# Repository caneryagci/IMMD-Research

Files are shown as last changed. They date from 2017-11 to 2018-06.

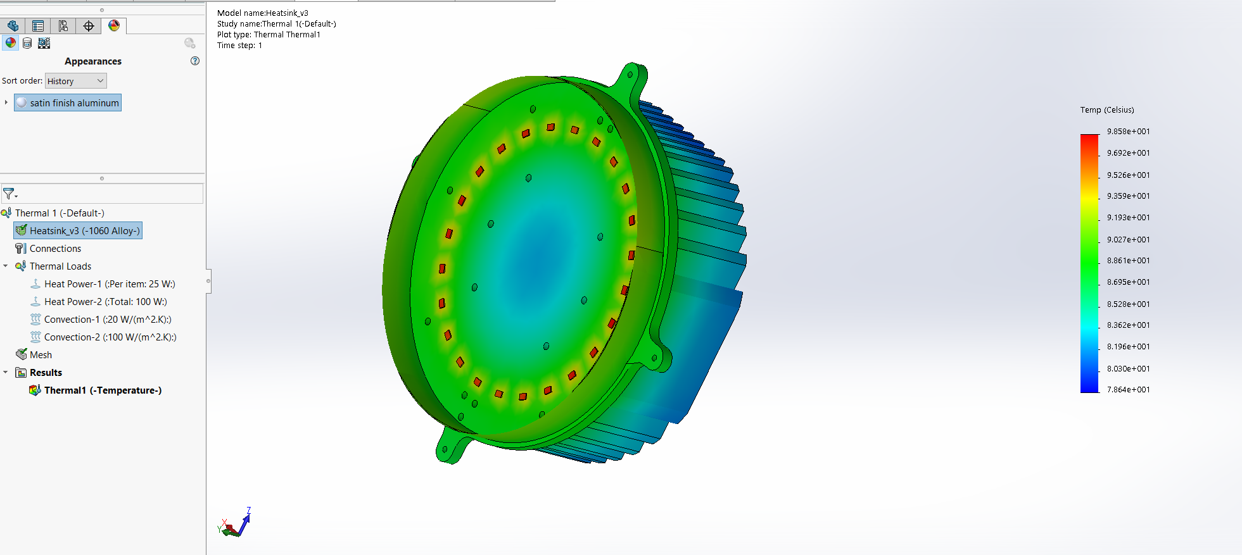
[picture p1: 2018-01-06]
Heatsink CAD Design/Design 3/Ekran Alıntısı.PNG

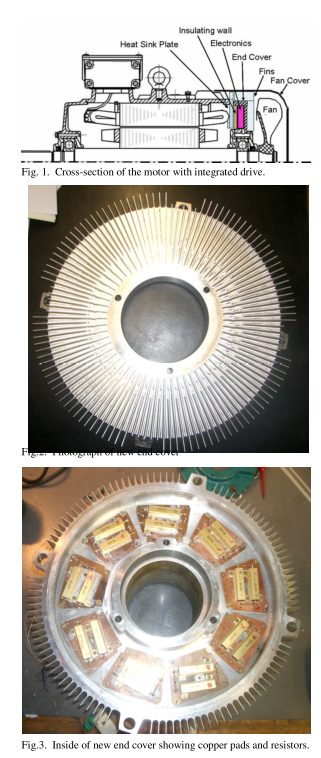
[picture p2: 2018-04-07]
Presentations/14.11.2017/Ekran Alıntısı.PNG

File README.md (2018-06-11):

# Thermal modeling, analysis and design of an Integrated Modular Motor Drive Application
The aim of the project is to obtain a thermal model of an integrated modular motor drive having different heat sources, analyze the thermal behavior of individual parts. A natural cooled heatsink is developed for the system. FEA and Steady-State Lumped Parameter analysis are implemented on Solidworks and MATLAB/Simulink.

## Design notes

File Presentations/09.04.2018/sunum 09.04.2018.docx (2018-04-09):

Steady-state Lumped Parameter Analysis

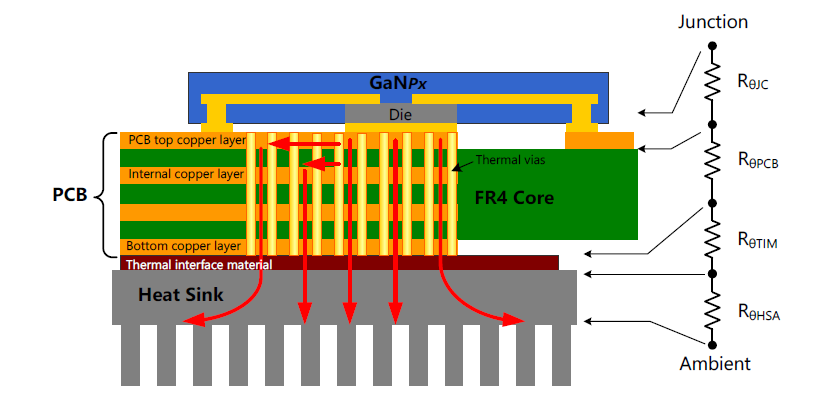
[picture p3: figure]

- 123 Thermal via (0.3mm diameter) , 6 Layer PCB, Rjc= 0.5 Ω , Rcpb= 4.5Ω(1.6mm & 6 layer), RTIM = 1.5 Ω

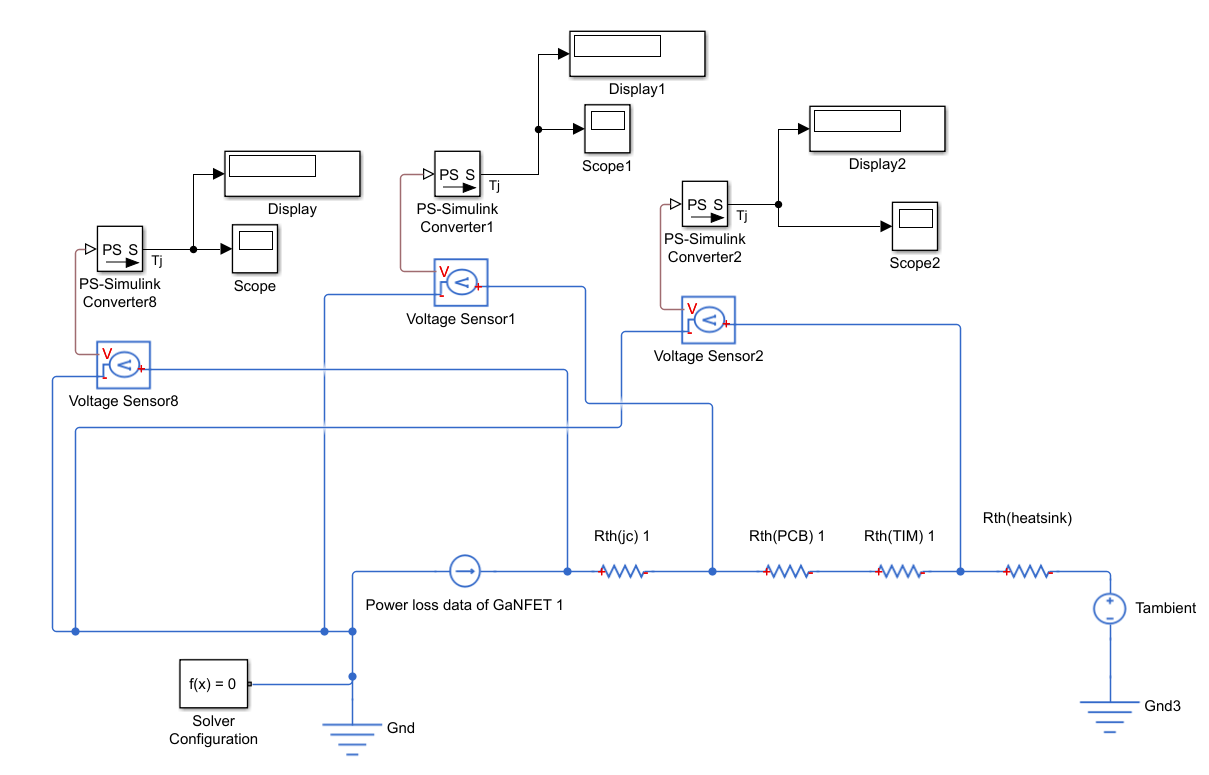
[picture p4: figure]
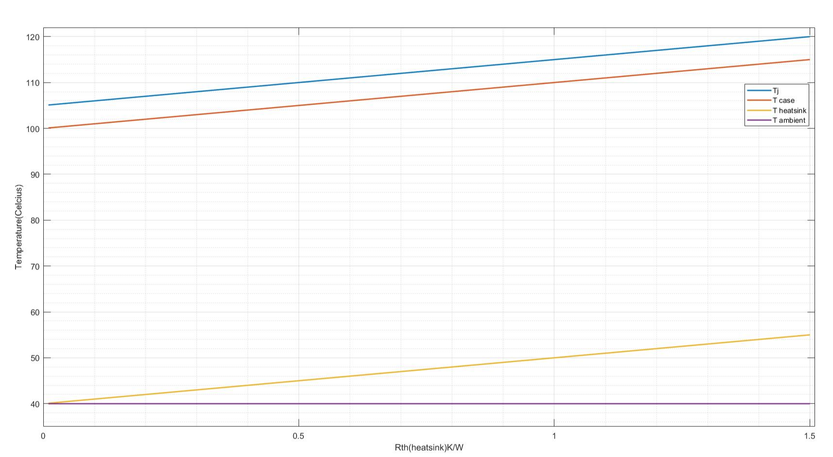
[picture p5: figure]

https://www.myheatsinks.com/calculate/thermal-resistance-plate-fin/

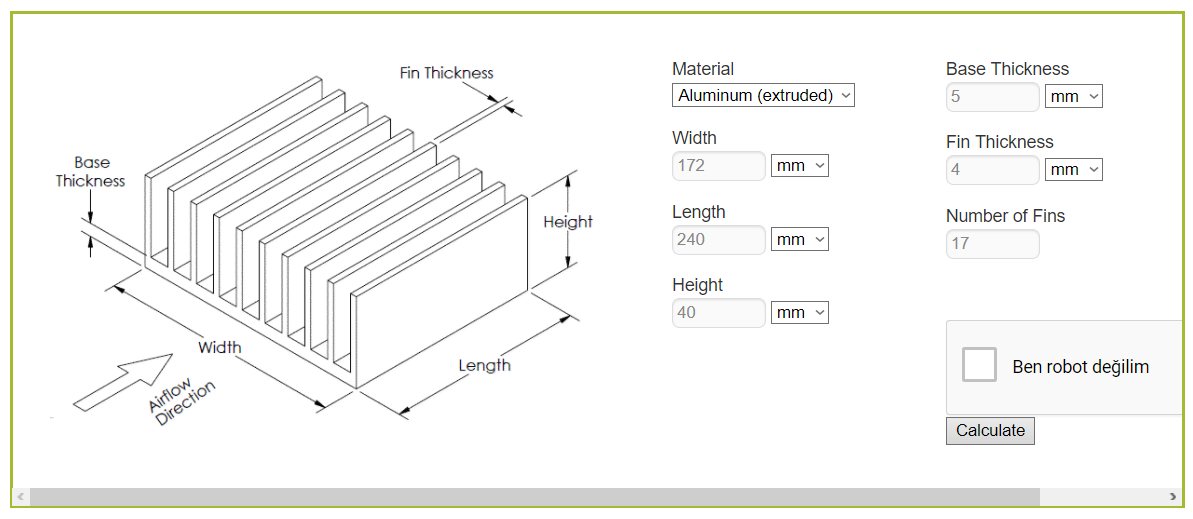
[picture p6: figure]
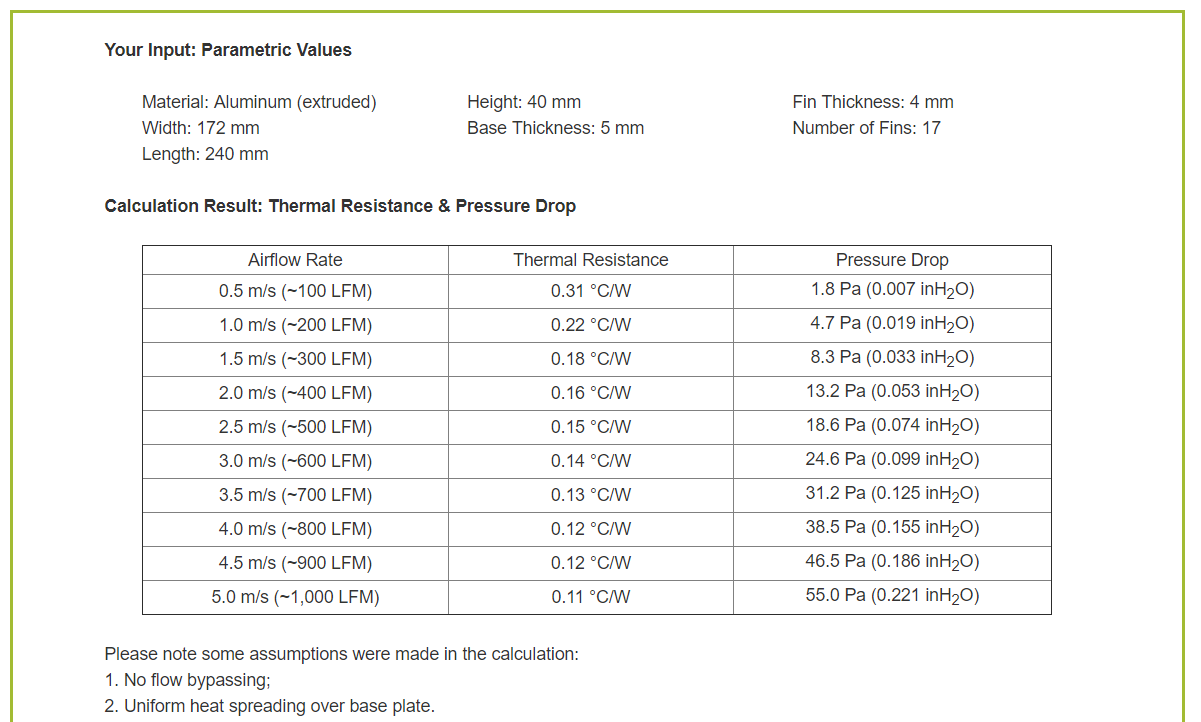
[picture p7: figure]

- The results changes between Rth (heatsink)= 0.25 - 0.45 ℃/W

FEA Analysis (Steady State)

If you think that GanFET is a black box with 0.5 Rjc ;

- L is the thickness (m) (thickness of the package and the thermal pad);
- A is the effective contact area (m²) (Area of the thermal pad) ;
- k is the conductivity of the box (W/(m*K))

R= L/(A.k) (1)

k=L/(A.R)=(0.440 x 10^(-3))/(2.667 x 10^(-3) x 0.5)=32.99 W/(m.K)

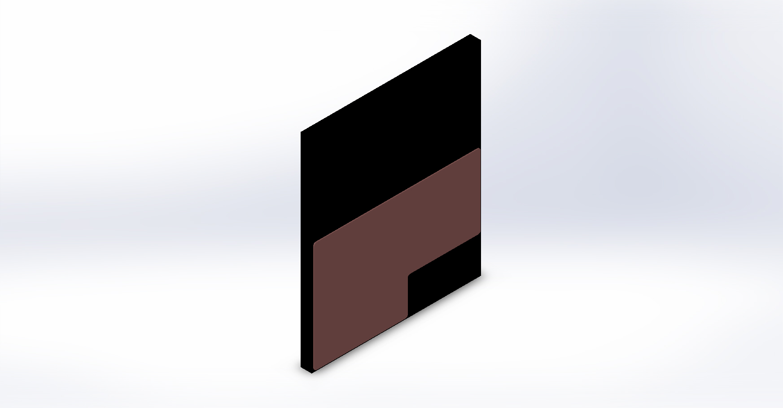
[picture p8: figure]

- For the most accurate Heat convection coefficients CFD analysis required.

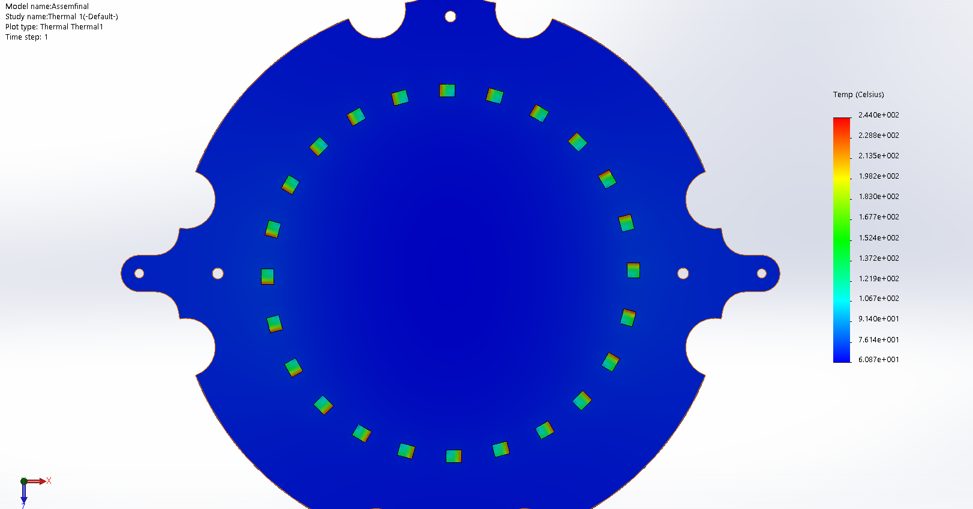
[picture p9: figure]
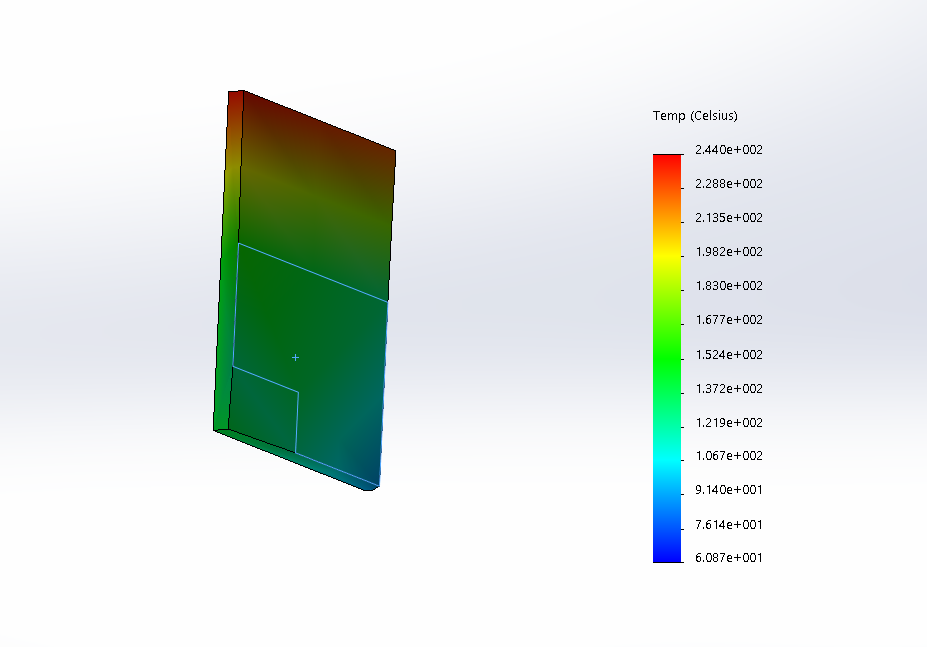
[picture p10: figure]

3D Design Engineers are divided into 2 groups;

- MCAD Design engineer (Mechanical)
- ECAD Design Engineer (Electronic)
- These engineers share the common file that is in IDF, EMN or STEP format.
- Each format has different features. (Based on the PCB layout and holes)
- IDF is the most common.

Following weeks;

- More accurate results
- FEA Transient Analysis

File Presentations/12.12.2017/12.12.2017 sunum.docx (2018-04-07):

- In fact, the heat-sink that was installed in this inverter has not a known value of thermal resistance. Anyway, to resolve this problem, is possible to measure this parameter measuring at the same time the losses and the temperature of the heat-sink for different values of losses. Once this parameter is found it is possible to simulate the real working condition in the model and to compare correctly the results.

[1] FOSSATO, F. (2014). Loss estimation in a voltage source inverter for electrical drives. University of Padua.

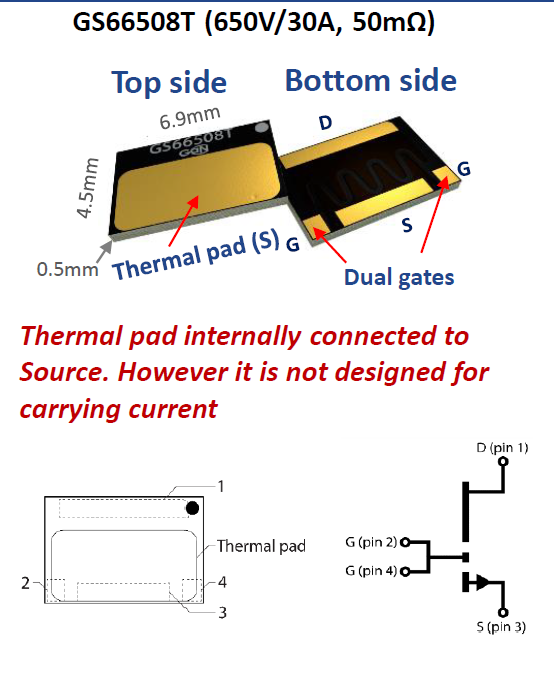
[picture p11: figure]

Figure: Top cooled

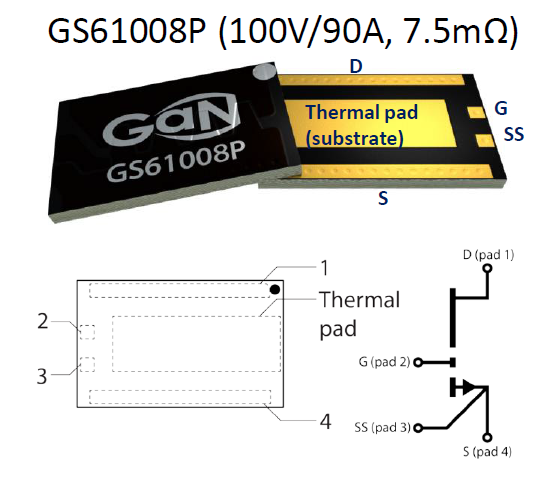
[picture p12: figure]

Figure: Bottom cooled

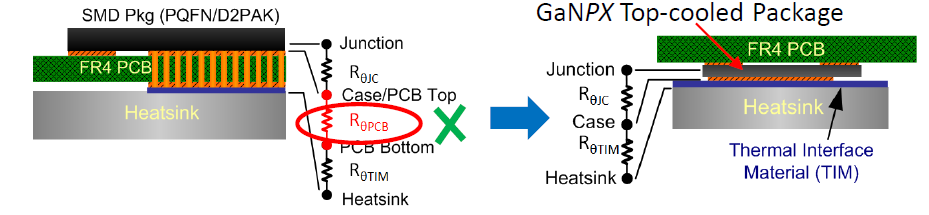
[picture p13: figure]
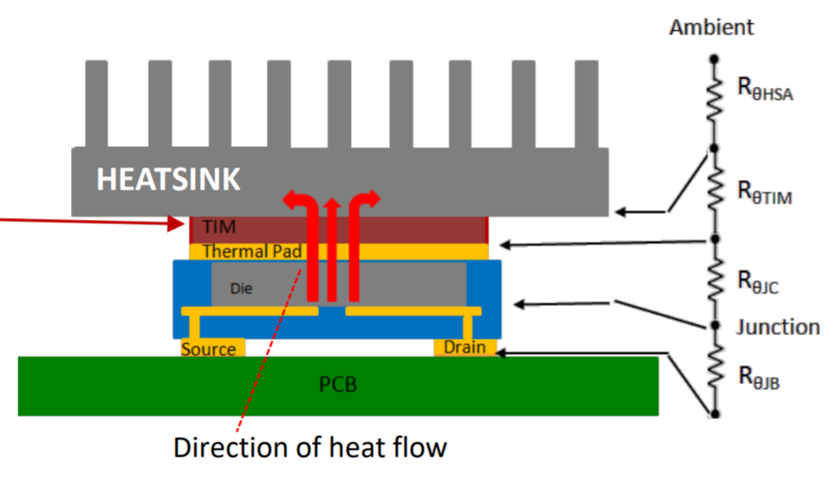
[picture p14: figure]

Figure: Top side cooling

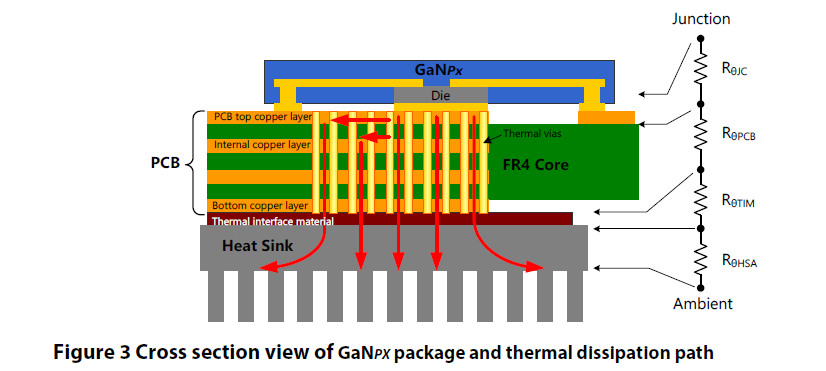
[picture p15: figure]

Figure:Bottom side cooling

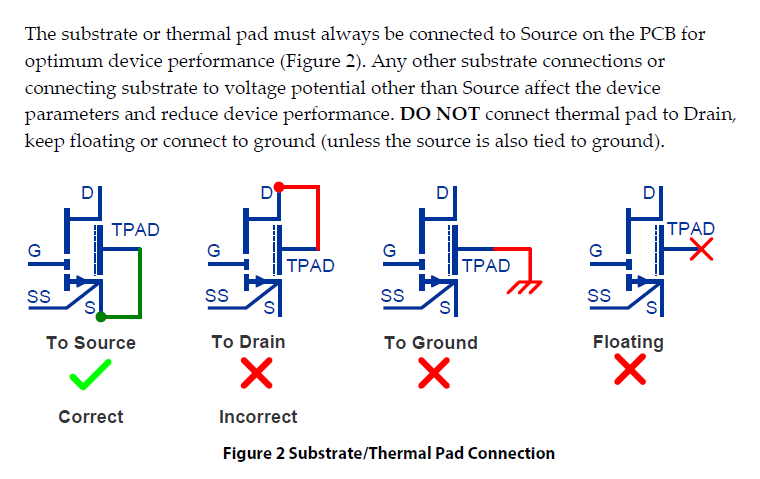
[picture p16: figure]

PCB thermal performance

1. Heat spreading copper pad

The top copper pad plays important role to conduct the heat from the small area under the device to larger area on the PCB. As such, the top copper layer must have sufficient thickness and area to provide enough heat spreading. It is recommended to always use 2 oz (56.7 g) or thicker copper on all layers. The internal and bottom layers also improve the heat spreading. The bottom copper pad serves as the contact surface to the heatsink or Thermal Interface Material (TIM) and it should have sufficient coverage to allow optimum heat transfer to the heatsink.

2. Thermal vias

The most effective way to improve vertical heat transfer for FR-4 PCB is to add plated through-hole thermal vias between conductive layers. Since FR-4 material has very low thermal conductivity, thermal vias design is one of the dominating factors for total PCB thermal resistance.

Below are some considerations for thermal vias design:

• Adding open plated through vias to the SMT pad (“Via In Pad”) is generally not a common practice as it may create the solder-wicking issue: the solder tends to be drained down into the vias during the reflow process and generates solder voids on the pad. Following steps can be taken to limit this problem:

o Use small via diameter. The surface tension of solder limits the amount of solder wicking on smaller vias. With 0.3 mm or smaller via diameter, the solder wicking can be reduced.

o Fill the vias with thermally conductive materials. It eliminates the solder wicking but adds cost and extra manufacturing step.

• 8 mil (0.2 mm) is typical minimum mechanical drilling size. 12 mil (0.3 mm) is more common and lower cost.

• IPC-6012 specifies minimum 0.8 mil (20 μm) copper plating thickness for Class 2 PCB and 1 mil (25 μm) is standard via plating thickness.

GaN Systems Simulation

The first step is to determine the right size for the heat spreading copper pad and how many vias are needed under the thermal pad.

The design constraint rule is that no vias are added towards the drain side in order to maintain the same clearance between thermal and Drain pads. Also the left edge of the copper pad keeps minimum 0.5 mm distance from Gate and Source-sense pads. There will be no vias added on the left side the package as that area is typically used for gate driver circuit.

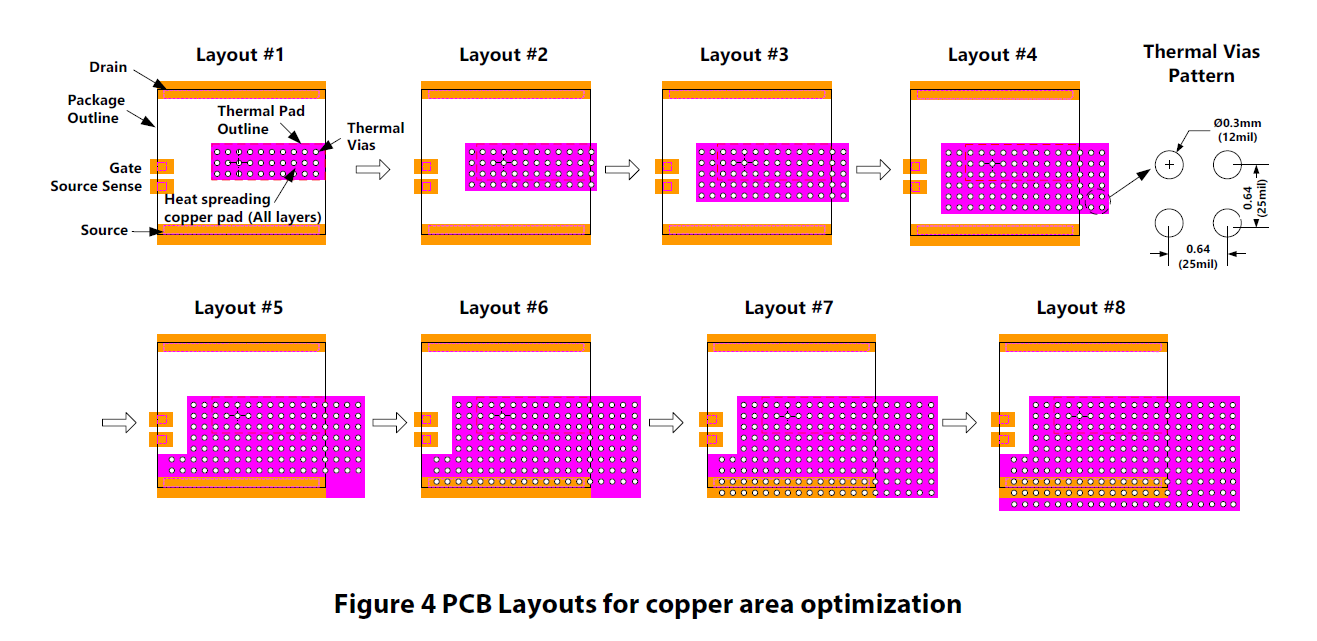
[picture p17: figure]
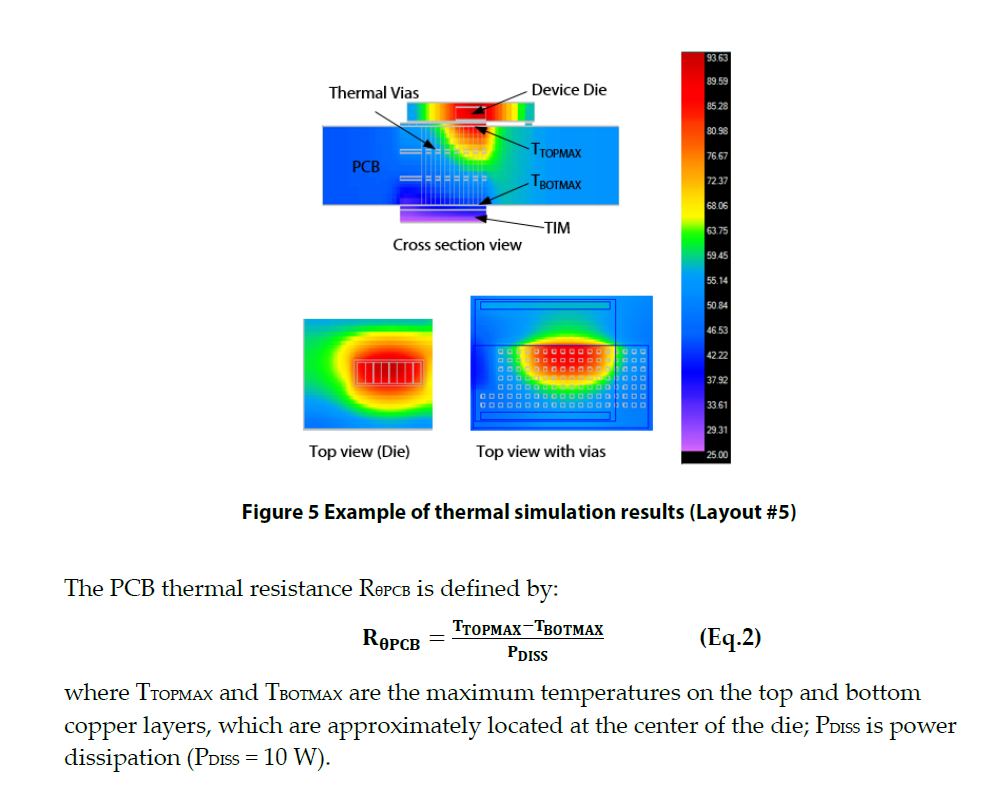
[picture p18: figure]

Figure: ElectroFlo® thermal analysis software was used for the thermal simulation

Both PCB and TIM thermal resistances decrease with the increasing of via numbers and copper area. When number of thermal vias increase from 30 to 210 (Layout #1 to #8), the PCB thermal resistance RθPCB drops almost 2.4 times from 11.5 °C/W to 4.8 °C/W. The TIM thermal resistance RθTIM also reduces about 3 times as the contact area increases.

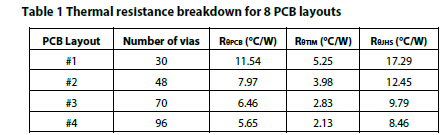
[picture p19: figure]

For optimum PCB thermal performance, it is recommended that the copper pad and thermal vias should cover at least 10x 5 mm area (50 mm2) under the thermal pad (or approximately 120 thermal vias), as shown in Figure 7.

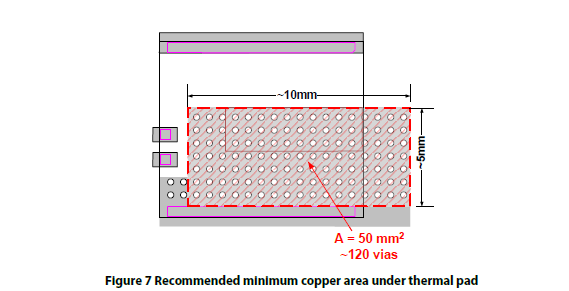
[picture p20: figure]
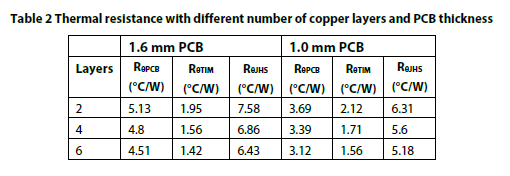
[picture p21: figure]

PCB thickness has

- less effect on TIM thermal performance and actually increases TIM thermal resistance by about 10 %.

- improvement on PCB thermal resistance

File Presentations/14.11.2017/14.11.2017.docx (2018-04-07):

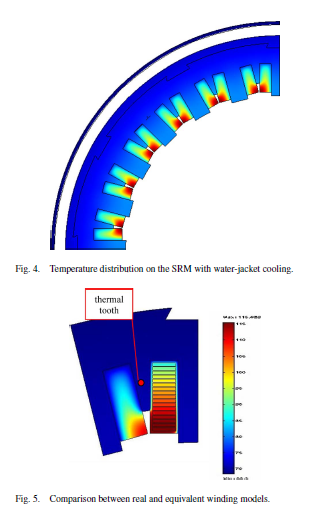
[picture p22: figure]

Since the copper–iron thermal resistance is the largest one in the thermal equivalent circuit of the machine, the reduction of the temperature gradient between copper and iron significantly reduces the total temperature gradient between the copper and the cooling fluid. For this reason, an auxiliary “thermal tooth” (Fig. 5) made of iron has been inserted to fill the triangle area: The iron triangles increase the thermal contact surface, improving the heat transmission through the coils sides, with only a little influence in torque production, if the height of a thermal triangle is sufficiently small.

[Tenconi, A., Profumo, F., Bauer, S. E., & Hennen, M. D. (2008). Temperatures evaluation in an integrated motor drive for traction applications. IEEE Transactions on Industrial Electronics, 55(10), 3619–3626. https://doi.org/10.1109/TIE.2008.2003099]


The thermal sink is common to all heat sources (Motor & Power Electronics).

In parallel configuration, the thermal flux paths are independent and do not influence each other. In practice, when the two heat sources are in close proximity this may require some thermal isolation.

Thermal isolation layer must be inserted to stop any thermal interference from the end-winding losses.

Series configuration would be difficult to achieve since the thermal gradient between the machine and the power electronics must be carefully managed so as not to overheat the devices.

The annular region surrounding the bearing housing on the end cover at the fan-end of the motor probably will be selected as being the most suitable for the drive components. Because the advantage that a flat area could be created to mount the components that could be largely isolated thermally from the rest of the motor and that could easily be cooled by air from the fan.

To prevent over heating of the end windings, an additional heat sink plate must be manufactured to fit between the end cover and the frame of the motor to conduct heat from the end region.

This heatsink plate effectively performed to replace the end cover in dissipating heat from the end region of the motor.

[Pickering, S., Thovex, F., Wheeler, P., & Bradley, K. (2006). Thermal Design of an Integrated Motor Drive. IECON 2006 - 32nd Annual Conference on IEEE Industrial Electronics, 4794–4799. https://doi.org/10.1109/IECON.2006.348109]

Heatsink

Fan

Power Electronics

Motor

Parallel Configuration

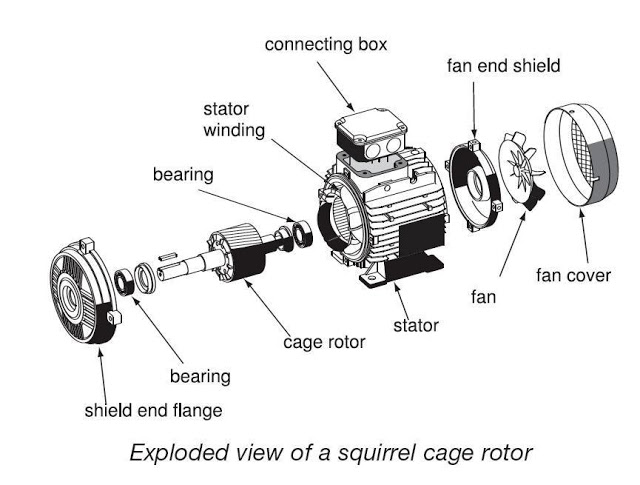
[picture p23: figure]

Thermal Insulation Layer

End Windings + Heatsink plate of the motor

Annular Heatsink

Power Electronics

Fan

Fan end shield

Variables:

- Fin density & length in the direction of the flow
- Fan Flow rate (velocity)
- Diameter of the heatsink in the direction perpendicular to the flow

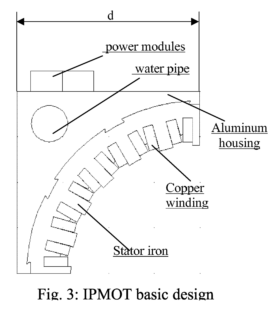
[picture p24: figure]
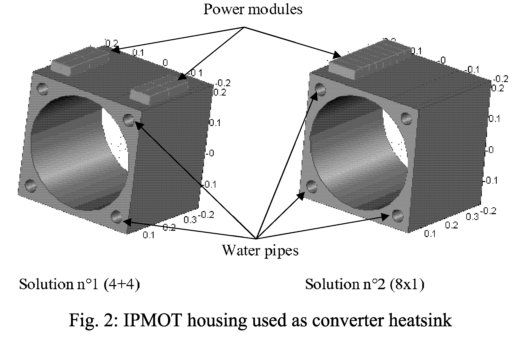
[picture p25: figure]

- Uses a rectangular profile machine with sunken cooling pipes in the machine core-back.
- The purpose of the flat edge profile of the machine is to provide a fixing surface directly on the machine body for the power electronic components.

[Farina, F., Rossi, D., Tenconi, A., Profumo, F., & Bauer, S. E. (2005). Thermal design of integrated motor drives for traction applications. 2005 European Conference on Power Electronics and Applications, 1–10. https://doi.org/10.1109/EPE.2005.219711]

PLAN:

1- Build a steady-state lump parameter circuit & simulate.
2- Determine a Rth value.
3- Design an annular heatsink by determining the critical parameters.
4- Simulate the heatsink by using thermal simulation software.

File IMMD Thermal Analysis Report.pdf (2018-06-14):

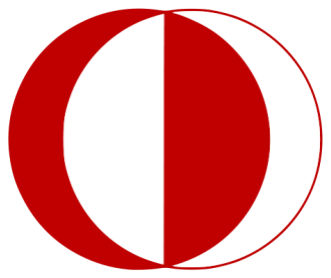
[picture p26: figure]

### MIDDLE EAST TECHNICAL UNIVERSITY

### DEPARTMENT OF ELECTRICAL AND ELECTRONICS ENGINEERING

### THERMAL MODELLING, ANALYSIS AND DESIGN OF AN INTEGRATED MODULAR MOTOR DRIVE APPLICATION

## Bekir Caner YAĞCI

## E:caneryagci1@gmail.com

P: +90 535 977 5608

14.06.2018

### Table of Contents

### 1. Introduction

The aim of the project is to obtain a thermal model of an integrated modular motor drive having different heat sources such as; power semiconductors, integrated circuits, capacitors, motor windings etc., and analyse the thermal behaviour of individual parts. A natural cooled heatsink is developed for the system. FEA and Steady-State Lumped Parameter analysis are implemented on SolidWorks and MATLAB/Simulink whether the designed heatsink reach the criteria.

In this report, theoretical and practical knowledge about the project is shared. Firstly, basic heat transfer mechanism, the ways of thermal analysis, and thermal resistance calculation is explained. Then, implemented analysis, their results, and practical challenges that encountered during analysis are discussed. Finally, supplementary links and articles are given in the references part.

### 2. Heat Transfer Mechanism & Thermal Analysis Methods

There are three mechanisms of heat transfer. These mechanisms are:

### 1. Conduction

- Conduction is responsible for heat transfer inside a solid body (or solid body to solid body assuming 100% conduction between).

### 2. Convection


- Convective heat transfer is the heat flow between a solid body and the surrounding fluid (either liquid or gas).


- It can be either natural or forced convection.

- The magnitude of the convection coefficient strongly depends on the medium (fluid) surrounding a solid body.


Figure 1: Convection coefficients for different media

### 3. Radiation

- Radiation heat transfer occurs between a solid body and the ambient or between two solid bodies without presence of any medium (fluid).
- Radiation is usually ignored since it has less effect than conduction, convection, and difficult to estimate.


Also, there are three methods of thermal analysis. These methods are:

### 1. Steady-State Lumped Parameter

- It is the method of thermal equivalent circuit of the interior of the system. This is analogous to an electric circuit, in that heat is generated by "current sources" that is the power loss and temperature is analogous to voltage. The rate of generation of heat in a source is measured in Watts. The heat flow rate, which is also measured in Watts, is analogous to current. Resistance is measured in ℃/W.
- It is the most straightforward method.
- Capacitive and the inductive effects in the system can be ignored to analyse the steady-state behaviour of the system. Thus, only a resistive circuitry could be analyse to see the worst case scenario of the system.

### 2. Finite Element Analysis (FEA)

- Well recognized tool used in the analysis of heat transfer problems.

- However, FEA can only analyze solid bodies and, by necessity thermal analysis with FEA is limited to conductive heat transfer. The other two types of heat transfer: convection and radiation must by approximated by boundary conditions.
- Requires a simulation program. (SolidWorks)

### 3. Computational Fluid Dynamics (CFD)

- Modeling all three mechanisms of heat transfer without arbitrary assumption requires a combined use of FEA and Computational Fluid Dynamics (CFD).
- CFD is the most complex computation method.
- Requires a simulation program. (SolidWorks Flow Simulation, ANSYS Fluid Dynamics, etc.)

Beside the lumped parameter method, the method to use depends on the heat transfer mechanisms that are taking place in the components that you are designing: conduction, convection, radiation or a combination of them. In addition, the level of accuracy you are willing to accept will also influence your decision.

The table below summarizes the method to use depending on the type of heat transfer mechanisms you are analyzing:

Table 1: The tool to use depending on the type of heat transfer mechanisms analysed


Thermal resistance calculation for heatsink

Fin geometry, fin length, number of fins, material (usually aluminium), cooling (natural or forced), heatsink geometry are effective on the thermal resistance of the heatsink.

For the calculation of the thermal resistance of the heatsink an online calculator at “https://www.myheatsinks.com/calculate/thermal-resistance-plate-fin/” is used to hardly estimate the thermal resistance of the heatsink selected. Also, the datasheets of the selected heatsinks are controlled if they meet the thermal resistance range calculated in the steady state analysis.

For the analytical calculation of the heatsink thermal resistance see reference [12].

### 3. Steady-State Lumped Parameter Analysis

To implement the steady-state analysis on Simulink environment thermal resistance values are selected from the Gan System’s own application notes. For more information see reference [5].

Given conditions are shown below;

- 120 Thermal via (0.3mm diameter)
- 6 Layer PCB
- Rjc= 0.5 Ω
- Rcpb= 4.5Ω(1.6mm & 6 layer)
- RTIM = 1.5 Ω


Figure 2: Bottom cooled GanFET connection

Figure 2 shows the lumped parameter circuitry of the bottom cooled GanFET. This circuit is drawn in Simulink environment as shown in the figure 3 with the given thermal resistance values. Then, voltage measurements are taken as temperature data from junction, case and heatsink. Ambient temperature is selected as 40 ℃. Finally, the Matlab code in appendix part is run to sweep the Rth(heatsink) parameter, and the results are plotted in figure 4.


Figure 3: Steady-state Simulink model

The result of the analysis is shown in figure 4. According to the figure 4, junction temperature is 110 ℃ when the thermal resistance of the heatsink is 0.5℃/W. Thus, the thermal resistance of the selected heatsink must be less than or equal to 0.5℃/W approximately.

Figure 4: Temperature results

For the simulation files see reference [11].

### 4. FEA Analysis

FEA analysis is implemented on SolidWorks environment. For the implementation of the analysis a 3D CAD figure of a circular heatsink with 40mm fin length, 5 mm baseplate thickness, 150 cm radius is drawn. Holes for mounting and places for windings are cut. Aluminium alloy is selected as material. For the CAD Drawings and the thermal analysis results see reference [11]. To learn more about the SolidWorks thermal analysis see reference [3], [4]

With SOLIDWORKS Simulation which uses finite element method, only heat transfer by conduction is modeled directly. Convection and radiation are modeled as boundary conditions. This is done by defining convection and/or radiation coefficients. Thus, a convection coefficient between 5-25 ℃/W must be defined to imitate natural cooling condition. Also, 6℃/W thermal resistance is defined via contact set to resemble the PCB and the TIM between each GanFET and the heatsink[4].


Figure 5: Overall heat dissipation on heatsink

The 3D drawing of the GanFET is available online or be see reference [11]. It can also be drawn with the given dimensions in the datasheet. For the thermal analysis only the thermal pad layer and the case is considered and the other layers such as drain, gate, soldering layers are ignored, since they increase the computation time and usually cause mesh errors.

GanFET is assumed to be a black box with a 0.5℃/W (create material with this specification) thermal resistance, and only conduction between the Gan’s and the heatsink is from the thermal pad in the implemented analyze. Figure 6 shows the heat dissipaton on GanFET. Blue line in figure 6 is the thermal pad, and it shows that the conducted part of the GanFET is cooled and the operation is possible with this heatsink as long as the proper conduction between the heatsink and the GanFET is implemented. However if the conduction between the heatsink and the GanFET is not proper GanFET can be heated up to 244 ℃.


Figure 6: Heat dissipation on a single GanFET

Problems of FEA in SolidWorks

The problem is that the SolidWorks is designed for mechanical systems and it is not very easy to reach the most accurate solution if you draw the electronic components such as GanFET, PCB, etc. in SolidWorks, since it is a bit complicated. My advice is to design the 3D Drawings of the electronic components in another simulation program such as Altium, and combine mechanical parts and the electronic parts via import/export in SolidWorks/CircuitWorks.

### 5. References

[1] Abebe, R., Vakil, G., Calzo, G. Lo, Cox, T., Gerada, C., & Johnson, M. (2015). FEA based thermal analysis of various topologies for Integrated Motor Drives (IMD). In IECON 2015 - 41st Annual Conference of the IEEE Industrial Electronics Society (pp. 001976–001981). IEEE. https://doi.org/10.1109/IECON.2015.7392390
[2] Pickering, S., Thovex, F., Wheeler, P., & Bradley, K. (2006). Thermal Design of an Integrated Motor Drive. IECON 2006 - 32nd Annual Conference on IEEE Industrial Electronics, 4794– 4799. https://doi.org/10.1109/IECON.2006.348109
[3] http://blogs.solidworks.com/solidworksblog/2017/04/use-fea-vs-cfd-thermal-analysis.html
[4] https://www.youtube.com/watch?v=Z8ymNlJoitw&list=WL&t=0s&index=45
[5] https://gansystems.com/design-center/application-notes/
[6] https://kupdf.com/embed/miller-tje-speed39s-electric-motors_58b2bb6a6454a7ce1eb1eaad.html?sp=%7Bstart%7D (https://kupdf.com/embed/miller-tje-speed39s-electric-motors_58b2bb6a6454a7ce1eb1eaad.html?sp=%7Bstart%7D)
[7] Mueller, S. I. (2005). MODEL AND DESIGN OF AN AIR-COOLED THERMAL MANAGEMENT SYSTEM FOR AN INTEGRATED MOTOR / CONTROLLER by.
[8] Inverter, S., Zhao, C., Member, S., Trento, B., Jiang, L., Member, S., … Langley, R. (2016). Design and Implementation of a GaN-Based , 4(3), 824–840.
[9] Wang, J., Li, Y., & Han, Y. (2015). Integrated Modular Motor Drive Design With GaN Power FETs. IEEE Transactions on Industry Applications, 51(c), 3198–3207. https://doi.org/10.1109/TIA.2015.2413380
[10] Tenconi, A., Profumo, F., Bauer, S. E., & Hennen, M. D. (2008). Temperatures evaluation in an integrated motor drive for traction applications. IEEE Transactions on Industrial Electronics, 55(10), 3619–3626. https://doi.org/10.1109/TIE.2008.2003099
[11] https://github.com/caneryagci/IMMD-Research
[12] Factor, P., & Perimeter, P. (n.d.). SIMPLIFIED METHOD FOR ESTIMATING HEAT SINK THERMAL RESISTANCE - Ө SA MATHEMATICAL FORMULA ANALYSES, 1–7.

Appendix: Steady-State Lumped Parameter Matlab Plot Code

Power_loss = 10;
Rth_jc = 0.5;
Rth_pcb = 4.5;
R_tim = 1.5;
T_ambient = 40;
ambient_t = ones(150,1)*40; junc_temp = zeros(150,1);
case_temp = zeros(150,1);
heatsink_t = zeros (150,1); resistance_h= zeros(150,1);

open_system('thermal_model'); for i= 1:1:150
Rth_heatsink = 0.01*i; %K/W sim('thermal_model');
resistance_h(i) = Rth_heatsink; junc_temp(i)= Tj(51,2);
case_temp(i) = T_case(51,2); heatsink_t (i) = T_heatsink(51,2);
end

plot(resistance_h,junc_temp,resistance_h,case_temp,resistance_h,heatsink_t,resistance_h,ambient_t,'L ineWidth',1.5);
grid on;
grid minor;
legend('Tj','T case','T heatsink','T ambient','Location','northeast'); xlabel('Rth(heatsink)K/W');
ylabel('Temperature(Celcius)');
ylim([35 122]);
xlim([0 1.51]);

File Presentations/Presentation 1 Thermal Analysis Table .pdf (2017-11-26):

Parameters | Values | Units
Rth (j-c) IGBT | 0.066 | K/W
Rth(j-c) FWD | 0.120 | K/W
Rth(case)1 | 0.000001 | K/W
Rth(case)2 | 0.000001 | K/W
Rth(case)3 | 0.000001 | K/W
Rth(paste) | 0.015 | K/W
Rth(heatsink) | 0.005 – 0.05 | K/W
Pss | 116.065 | W
Psw | 116.18 | W
Total Power loss of each IGBT | 232.25 | W
PDC | 30.54 | W
Prr | 11.25 | W
Total Power loss of each FWD | 41.79 | W
Esw(on) | 41 | mJ
Esw(off) | 32 | mJ
Fsw | 5 | kHz
Icp | 300 | A
VCE(sat) | 2 | V
VEC | 1.8 | V

D 0.85
θ | 25.842 | Degrees
Irr | 200 | A
trr | 300 | ns
VCE(pk) | 300 | V


Pss: Steady-state loss per switching IGBT

Psw: Switching loss per switching IGBT

PDC: Steady-state loss per diode

Prr: Recovery loss per diode

Rth (j-c): thermal resistance junction to case

Tj IGBT 1U: Junction temperature of the upper IGBT of the phase 1

Tj IGBT 1L: Junction temperature of the lower IGBT of the phase 1

Tj FWD 1U: Junction temperature of the upper free-wheeling diode of the phase 1

Tj FWD 1L: Junction temperature of the lower free-wheeling diode of the phase 1

Data | Rth(heatsink) K/W | Tj IGBT (celcius) | Tj FWD(celcius) | T(case) | T(heatsink) | Ta
1 | 0.005 | 75.64 | 100.8 | 72.88 | 48.22 | 40
2 | 0.006 | 77.29 | 102.4 | 74.53 | 49.87 | 40
3 | 0.007 | 78.93 | 104 | 76.17 | 51.5 | 40
4 | 0.008 | 80.58 | 105.7 | 77.82 | 53.15 | 40
5 | 0.009 | 82.22 | 107.3 | 79.46 | 54.8 | 40
6 | 0.010 | 83.66 | 109 | 81.11 | 56.44 | 40
7 | 0.012 | 87.15 | 112.3 | 84.39 | 59.73 | 40
8 | 0.015 | 92.09 | 117.2 | 89.33 | 64.66 | 40
9 | 0.017 | 95.37 | 120.5 | 92.62 | 67.95 | 40
10 | 0.020 | 100.3 | 125.4 | 97.55 | 72.88 | 40
11 | 0.022 | 103.6 | 128.7 | 100.8 | 76.17 | 40
12 | 0.025 | 108.5 | 133.6 | 105.8 | 81.11 | 40
13 | 0.027 | 111.8 | 136.9 | 109.1 | 84.39 | 40
14 | 0.030 | 116.7 | 141.9 | 114 | 89.33 | 40
15 | 0.032 | 120 | 145.1 | 117.3 | 92.62 | 40
16 | 0.035 | 125 | 150 | 122.2 | 97.55 | 40
17 | 0.037 | 128.3 | 153.4 | 125.5 | 100.8 | 40
18 | 0.040 | 133.2 | 158.3 | 130.4 | 105.8 | 40
19 | 0.042 | 136.5 | 161.6 | 133.7 | 109.1 | 40
20 | 0.045 | 141.4 | 166.5 | 138.7 | 114 | 40
21 | 0.047 | 144.7 | 169.8 | 141.9 | 117.3 | 40
22 | 0.050 | 149.6 | 174.7 | 146.9 | 122.2 | 40


- Tj(FWD) = 125.4 ℃ when Rth(heatsink) = 0.02 K/W

### Heatsink Selection



### QUESTION ?



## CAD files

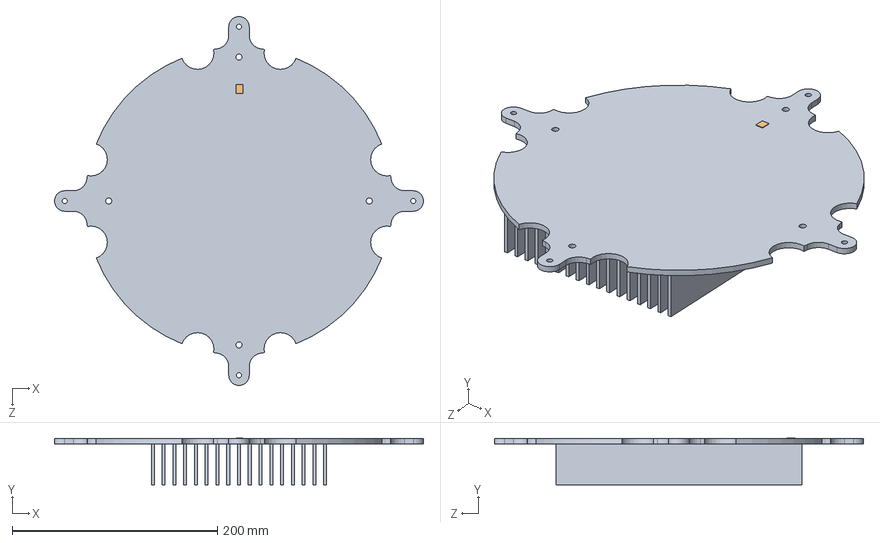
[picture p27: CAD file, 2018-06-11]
FEA Analysis 2/Assem3.SLDASM
360.0 x 45.5 x 360.0 mm
Heatsink2
Package
PCB Bottom CDMM

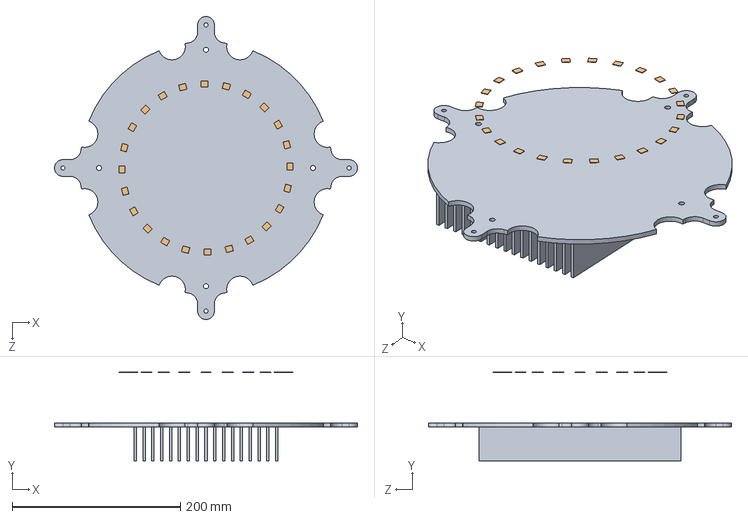
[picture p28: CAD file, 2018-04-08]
FEA Analysis 1/Assemfinal.SLDASM
360.0 x 105.4 x 360.0 mm
Heatsink
Black Box x 24

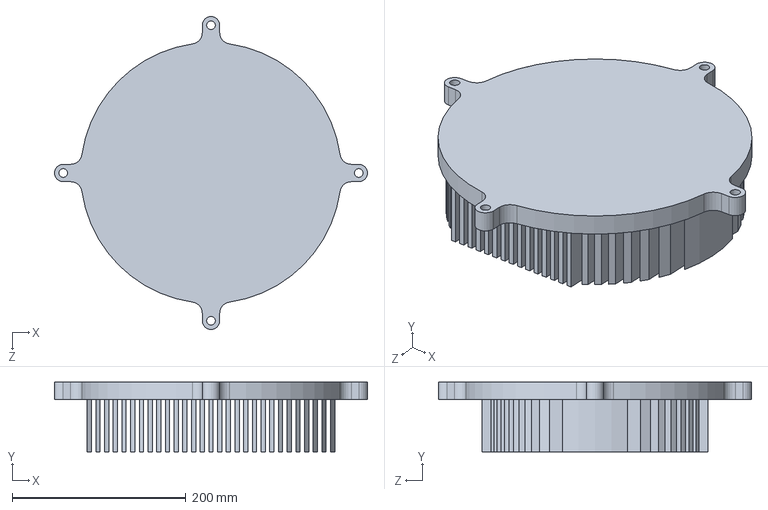
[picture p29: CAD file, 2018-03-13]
Heatsink CAD Design/Design 1/Heatsink_v1.SLDPRT
360.0 x 80.0 x 360.0 mm

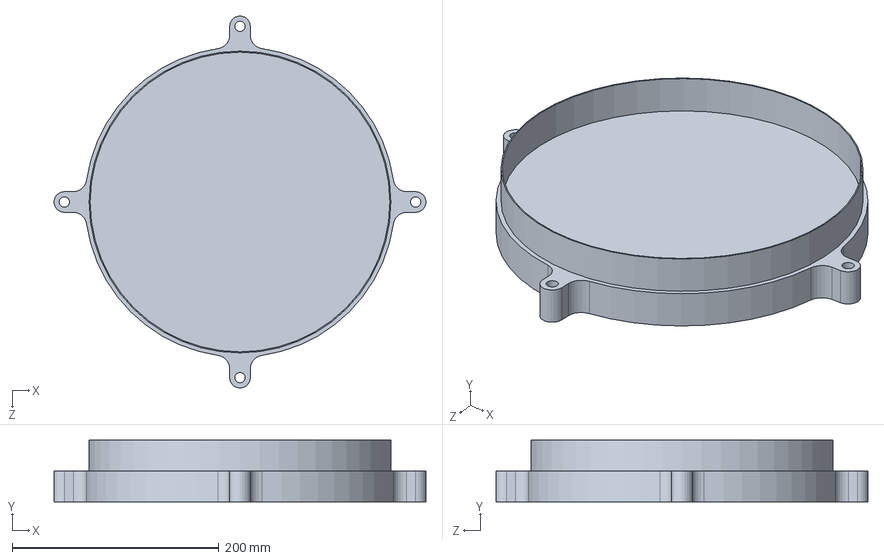
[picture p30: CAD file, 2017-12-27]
Heatsink CAD Design/Design 2/Heatsink2.SLDPRT
360.0 x 60.0 x 360.0 mm

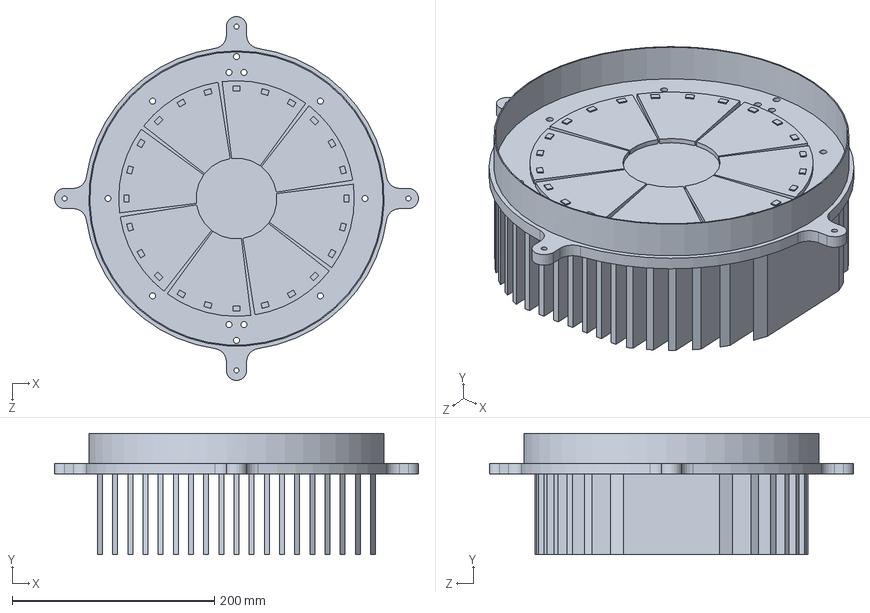
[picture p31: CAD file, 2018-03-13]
Heatsink CAD Design/Design 3/Heatsink_v3.SLDPRT
360.0 x 120.0 x 360.0 mm

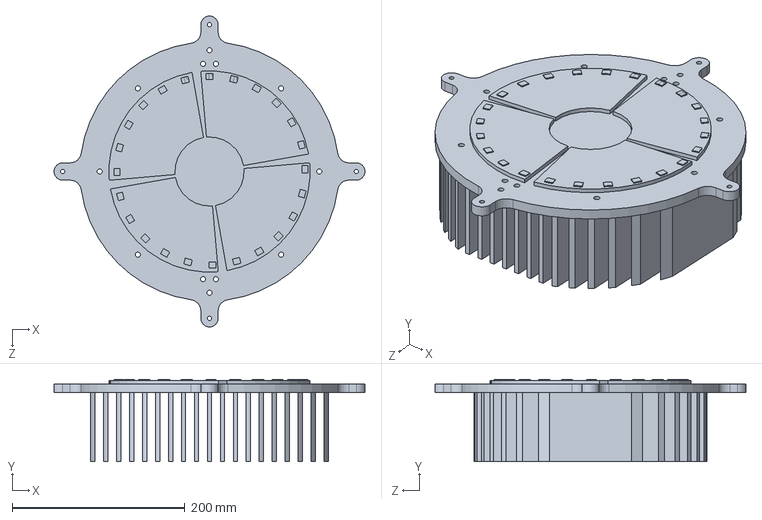
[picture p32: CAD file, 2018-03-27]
Heatsink CAD Design/Design 4/Heatsink_v4.SLDPRT
360.0 x 95.0 x 360.0 mm

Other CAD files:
FEA Analysis 1/Assem1.SLDASM
FEA Analysis 1/Package.sldprt
GS66508B GAN CAD Drawing/Soldermask Bottom CDMM.sldprt
FEA Analysis 1/Soldermask Top.sldprt
FEA Analysis 2/Package.sldprt
Heatsink CAD Design/Design 3/Untitled.dwg
FEA Analysis 1/Soldermask Bottom CDMM.sldprt
FEA Analysis 2/Soldermask Top.sldprt
GS66508B GAN CAD Drawing/Soldermask Top.sldprt
FEA Analysis 2/PCB Bottom CDMM.sldprt
GS66508B GAN CAD Drawing/PCB Bottom CDMM.sldprt
FEA Analysis 1/PCB Bottom CDMM_1.sldprt
FEA Analysis 1/Black Box.SLDPRT
FEA Analysis 1/GS66508B.SLDASM
FEA Analysis 1/GS66508B.STEP
FEA Analysis 1/Heatsink.SLDPRT
FEA Analysis 1/PCB Bottom CDMM.sldprt
FEA Analysis 1/Paket.SLDPRT
FEA Analysis 2/Gan.SLDASM
FEA Analysis 2/Gan.STEP
FEA Analysis 2/Heatsink2.SLDPRT
FEA Analysis 2/Soldermask Bottom CDMM.sldprt
GS66508B GAN CAD Drawing/GS66508B.SLDASM
GS66508B GAN CAD Drawing/GS66508B.STEP
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

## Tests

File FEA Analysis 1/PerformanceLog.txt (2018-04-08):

Preparing to transfer data:  0 hr 0 min 0 sec
Processing material properties:  0 hr 0 min 0 sec
Processing element groups:  0 hr 0 min 0 sec
Processing drop test gap nodes:  0 hr 0 min 0 sec
Updating thickness for shell regions:  0 hr 0 min 0 sec
Processing rconst for elements:  0 hr 0 min 0 sec
Processing egroups:  0 hr 0 min 0 sec
Transferring loads and boundary conditions:  0 hr 0 min 0 sec
Generating body pairs to check contact:  0 hr 0 min 0 sec
Generating contacts:  0 hr 0 min 0 sec
Number of Contacts: 24
Transfer SL1 data:  0 hr 0 min 0 sec
Generate simplified contact data:  0 hr 0 min 0 sec
Generate more accurate contact data:  0 hr 0 min 1 sec
Number of contact data: 3538
Transfer beam/joint contact data:  0 hr 0 min 0 sec
Transferring other special loads:  0 hr 0 min 0 sec
Transferring bearing loads:  0 hr 0 min 0 sec
Writing Data:  0 hr 0 min 0 sec
Transferring analysis options:  0 hr 0 min 0 sec
Total midsurf mapping:  0 hr 0 min 0 sec

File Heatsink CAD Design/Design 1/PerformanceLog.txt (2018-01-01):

Mesh Preparation:  0 hr 0 min 0 sec
Standard solid mesh bolt head imprint and hard point processing:  0 hr 0 min 0 sec
Standard solid mesh total preparation including imprint:  0 hr 0 min 0 sec
Standard surface meshing for Solid Mesh:  0 hr 0 min 1 sec
Standard volume meshing for Solid Mesh:  0 hr 0 min 13 sec
Standard solid mesh arranging data:  0 hr 0 min 0 sec
Standard solid mesh total:  0 hr 0 min 15 sec
Beam mesh:  0 hr 0 min 0 sec
Preparing to transfer data:  0 hr 0 min 16 sec
Processing material properties:  0 hr 0 min 0 sec
Processing element groups:  0 hr 0 min 0 sec
Processing drop test gap nodes:  0 hr 0 min 0 sec
Updating thickness for shell regions:  0 hr 0 min 0 sec
Processing rconst for elements:  0 hr 0 min 0 sec
Processing egroups:  0 hr 0 min 0 sec
Transferring loads and boundary conditions:  0 hr 0 min 0 sec
Generating body pairs to check contact:  0 hr 0 min 0 sec
Generating contacts:  0 hr 0 min 0 sec
Number of Contacts: 0
Transfer SL1 data:  0 hr 0 min 0 sec
Generate simplified contact data:  0 hr 0 min 0 sec
Generate more accurate contact data:  0 hr 0 min 0 sec
Number of contact data: 0
Transfer beam/joint contact data:  0 hr 0 min 0 sec
Transferring other special loads:  0 hr 0 min 0 sec
Transferring bearing loads:  0 hr 0 min 0 sec
Writing Data:  0 hr 0 min 0 sec
Transferring analysis options:  0 hr 0 min 0 sec
Total midsurf mapping:  0 hr 0 min 0 sec

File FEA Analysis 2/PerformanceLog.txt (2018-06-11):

Mesh Preparation:  0 hr 0 min 0 sec
Standard solid mesh assembly imprint:  0 hr 0 min 0 sec
Standard solid mesh bolt head imprint and hard point processing:  0 hr 0 min 0 sec
Standard solid mesh total preparation including imprint:  0 hr 0 min 0 sec
Standard surface meshing for Solid Mesh:  0 hr 0 min 0 sec
Standard volume meshing for Solid Mesh:  0 hr 0 min 0 sec
Standard surface meshing for Solid Mesh:  0 hr 0 min 0 sec
Standard volume meshing for Solid Mesh:  0 hr 0 min 0 sec
Standard surface meshing for Solid Mesh:  0 hr 0 min 0 sec
Standard volume meshing for Solid Mesh:  0 hr 0 min 0 sec
Standard surface meshing for Solid Mesh:  0 hr 0 min 0 sec
Standard volume meshing for Solid Mesh:  0 hr 0 min 0 sec
Standard surface meshing for Solid Mesh:  0 hr 0 min 0 sec
Standard volume meshing for Solid Mesh:  0 hr 0 min 0 sec
Standard surface meshing for Solid Mesh:  0 hr 0 min 0 sec
Standard volume meshing for Solid Mesh:  0 hr 0 min 10 sec
Standard surface meshing for Solid Mesh:  0 hr 0 min 2 sec
Standard volume meshing for Solid Mesh:  0 hr 0 min 10 sec
Standard solid mesh total:  0 hr 0 min 14 sec
Beam mesh:  0 hr 0 min 0 sec
Mesh Preparation:  0 hr 0 min 0 sec
Standard solid mesh assembly imprint:  0 hr 0 min 0 sec
Standard solid mesh bolt head imprint and hard point processing:  0 hr 0 min 0 sec
Standard solid mesh total preparation including imprint:  0 hr 0 min 0 sec
Standard surface meshing for Solid Mesh:  0 hr 0 min 0 sec
Standard volume meshing for Solid Mesh:  0 hr 0 min 0 sec
Standard surface meshing for Solid Mesh:  0 hr 0 min 0 sec
Standard volume meshing for Solid Mesh:  0 hr 0 min 0 sec
Standard surface meshing for Solid Mesh:  0 hr 0 min 0 sec
Standard volume meshing for Solid Mesh:  0 hr 0 min 0 sec
Standard surface meshing for Solid Mesh:  0 hr 0 min 0 sec
Standard volume meshing for Solid Mesh:  0 hr 0 min 0 sec
Standard surface meshing for Solid Mesh:  0 hr 0 min 0 sec
Standard volume meshing for Solid Mesh:  0 hr 0 min 0 sec
Standard surface meshing for Solid Mesh:  0 hr 0 min 1 sec
Standard volume meshing for Solid Mesh:  0 hr 0 min 0 sec
Standard solid mesh total:  0 hr 0 min 4 sec
Beam mesh:  0 hr 0 min 0 sec

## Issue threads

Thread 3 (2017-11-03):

Rth_heatsink Parameter Sweep

caneryagci, 2017-11-03:
Merhaba Hocam,
Simulink modelimdeki  "Rth_heatsink" bloğunun değerini m.file üzerinden sweep ederek farklı Rth_heatsink (x-axis)değerleri için Tj IGBT, Tj FWD, etc. (y-axis) grafiği oluşturmaya çalışıyorum.

Bunun için "set_param" fonksiyonunu kullanarak simulink modelimi for loop içinde döndürmeye çalıştım ama errorlerden kurtulamadım.

1-Simulink parametremin değerini tek bir run içinde değiştirebilir miyim ? ya da
2-Yapmak istediğim grafiği nasıl oluşturabilirim?
3-Logging'i nasıl kullanabilirim?

Şuan için Rth (heatsink) değerini tek tek elimle girip sırayla run ederek değerlerden excel dosyası oluşturup plot etmeyi düşünüyorum ama eminim ki daha verimli bir yol vardır :D

@ozank @mesutto

mesutto, 2017-11-07:
Selam Caner,

Ben bu issue'yu atlamışım kusura bakma şimdi gördüm.

Ekstra fonksiyon kullanmana gerek yok. .m file içinde Rth_hs = x şeklinde assign edip, simulasyon modelinde de direnç değerine Rth_hs yazarsan simulink onu tanıyacaktır. Sonra .m file'da "sim" fonksiyonu ile simulasyonu çağırabilirsin, ve simulasyon sonuçlarını workspace'e attıktan sonra o iterasyondaki değeri bir array'e kaydedebilirsin. Böyle tüm iterasyonlar bittiğinde her iterasyondaki Tj değerlerinin kaydedildiği bir array'in olmuş olacak.

Evet, her zaman elle yapmaktan daha verimli bir yol var. :) Bugün toplantıda detaylı bakarız.

Eline sağlık !

Closed 2018-06-11.

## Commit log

2017-04-04 I am not sure if there must be capacitors in the model or there should be diode thermal resistors instead.
2017-04-04 More detailed model. Per module thermal analysis must be done to choose a proper heat sink.
2017-04-16 I could not obtain R and C values of the fourth order foster equivalent thermal model. Hence, decided to use steady state model. Power loss calculations will be done.
2017-10-21 New resistive thermal model added but not finished.
2017-10-23 I learned that the simscape models can not be connected with the simulink models so I tried to use voltage sensor instead of voltage measurment model and it has different signal application.
2017-10-24 Thermal resistance and power loss values are updated.
2017-10-30 m.file for power loss calculations and thermal data variables is written. Thermal model updated.
2017-11-06 Rth(heatsink) vs. Junction temperatures plot and documentation
    [temperatures.xlsx]
2017-11-26 Heatsink CAD design
    [radiateur_IMMD.SLDPRT]
2017-12-27 Heatsink CAD Drawing
    [Heatsink1.SLDPRT, Heatsink2.SLDPRT, radiateur_IMMD.SLDPRT]
2018-01-01 Heatsink version 3
    [Heatsink_v1.SLDPRT, Heatsink_v3.SLDPRT]
2018-01-06 Heatsink Design & Analysis
    [Heatsink_v3.SLDPRT]
2018-02-27 design update
    [Heatsink_v3.SLDPRT, Untitled.dwg]
2018-03-27 Design 5
    [Heatsink_v4.SLDPRT]
2018-04-07 Sunum 09.04.2018
    [Assem1.SLDASM, GS66508B.SLDASM, GS66508B.STEP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]
2018-04-08 FEA analysis
    [Assem1.SLDASM, Assemfinal.SLDASM, Black Box.SLDPRT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]
2018-06-11 File Arrangement
    [Assem1.SLDASM, Assem3.SLDASM, Assemfinal.SLDASM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]
